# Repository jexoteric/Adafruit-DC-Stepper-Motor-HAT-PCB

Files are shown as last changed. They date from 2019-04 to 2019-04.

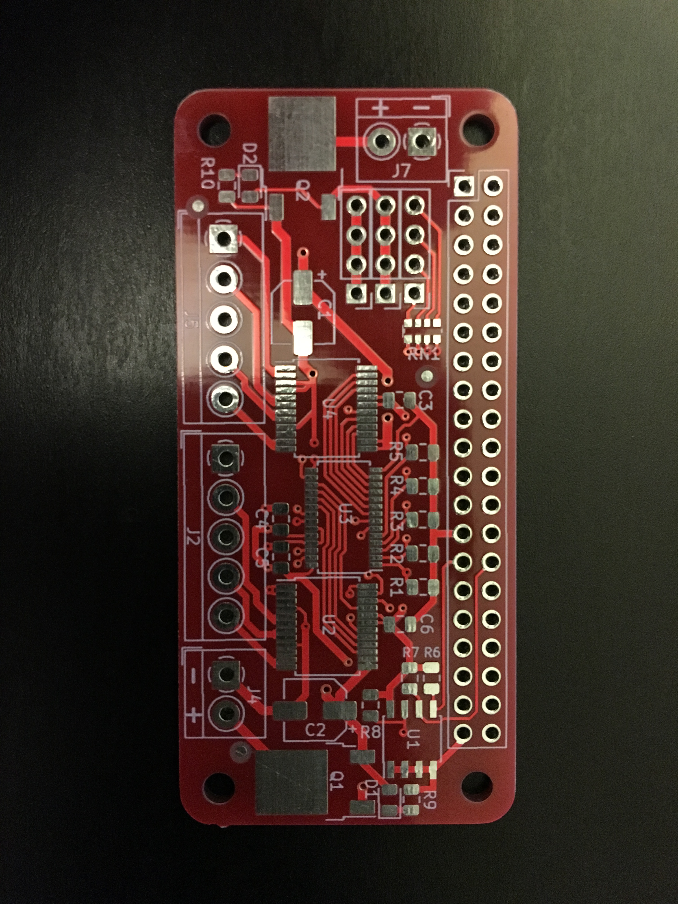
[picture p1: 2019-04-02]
IMG_0204.JPG

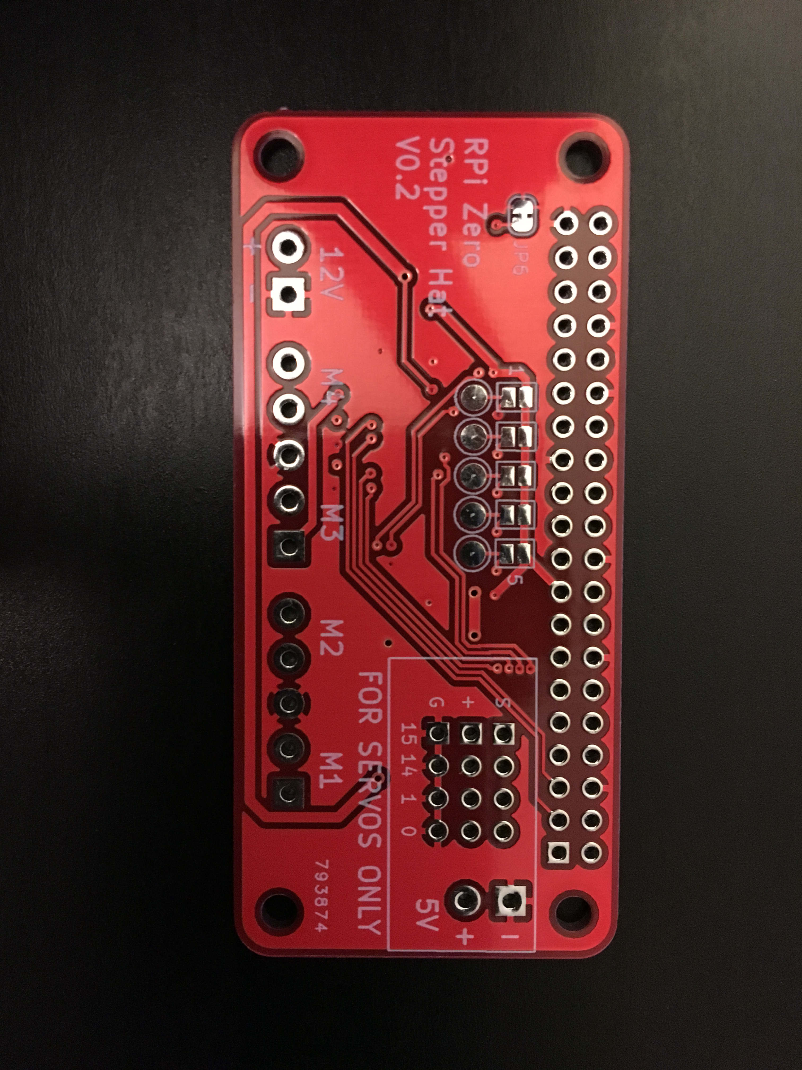
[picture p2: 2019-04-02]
IMG_0206.JPG

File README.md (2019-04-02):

# Raspberry Pi Zero DC and Stepper motor hat
Creating a more compact version of the Adafruit DC Stepper motor hat, with the goal of 100% compatability. The only real changes are there is no prototyping area or breakout of the pi pins. Optionally, the four extra PWM pins are now set up to control servos, using a seperate 5V power supply.

Programming with this board should be 100% identical to programming with the original Adafruit design linked below.

For more details, check out the product page at

   * https://www.adafruit.com/products/2348

Adafruit invests time and resources providing this open source design, 
please support Adafruit and open-source hardware by purchasing 
products from Adafruit!

Original board designed by Adafruit Industries.  
Creative Commons Attribution, Share-Alike license, check license.txt for more information
All text above must be included in any redistribution

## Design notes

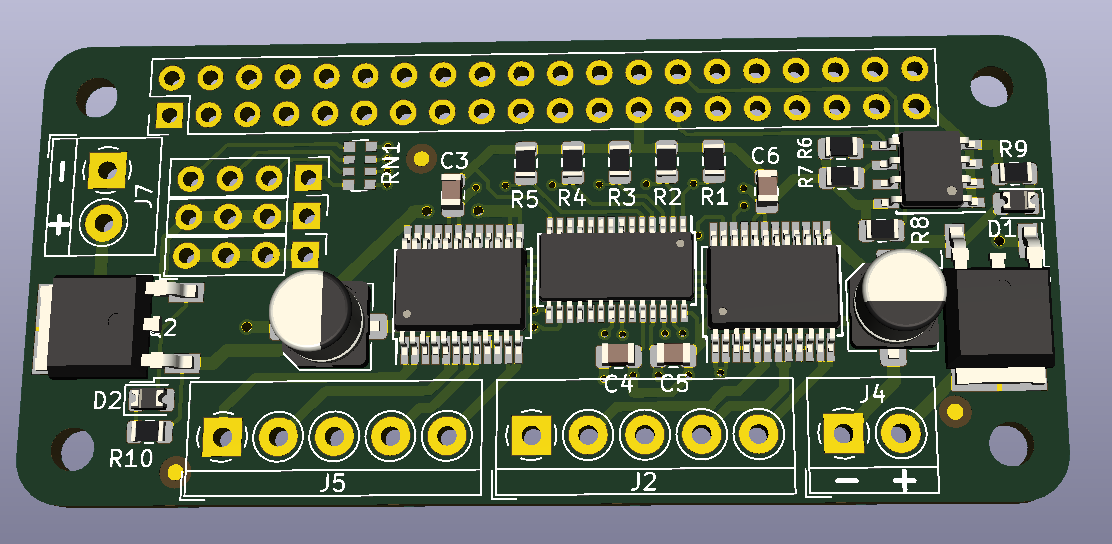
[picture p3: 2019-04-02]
pi_zero_stepper.PNG

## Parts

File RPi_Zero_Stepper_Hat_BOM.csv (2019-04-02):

Manufacturer Part Number | Manufacturer | Digi-Key Part Number | Customer Reference | Reference Designator | Packaging | Quantity | Unit Price | Extended Price | Description
EEE-1CA470WAR | Panasonic Electronic Components | PCE4588CT-ND | 47uF/16v | C1, C2 | Cut Tape (CT) | 2 | 0.38 | $0.76 | CAP ALUM 47UF 20% 16V SMD
CC0805ZKY5V6BB106 | Yageo | 311-1355-1-ND | 10uF | C3, C6 | Cut Tape (CT) | 2 | 0.28 | $0.56 | CAP CER 10UF 10V Y5V 0805
CC0805ZRY5V9BB104 | Yageo | 311-1361-1-ND | 0.1uF | C4, C5 | Cut Tape (CT) | 2 | 0.13 | $0.26 | CAP CER 0.1UF 50V Y5V 0805
17-21SYGC/S530-E2/TR8 | Everlight Electronics Co Ltd | 1080-1500-1-ND | GREEN | D1, D2 | Cut Tape (CT) | 2 | 0.3 | $0.60 | LED YELLOW/GREEN CLEAR 0805 SMD
AOD417 | Alpha & Omega Semiconductor Inc. | 785-1106-1-ND | AOD417 | Q1,Q2 | Cut Tape (CT) | 2 | 0.56 | $1.12 | MOSFET P-CH 30V 25A TO252
RNCF0805DTE10K0 | Stackpole Electronics Inc | RNCF0805DTE10K0CT-ND | 10K | R1, R2, R3, R4, R5 | Cut Tape (CT) | 5 | 0.17 | $0.85 | RES 10K OHM 0.5% 1/8W 0805
RC0805FR-073K9L | Yageo | 311-3.90KCRCT-ND | 3.9K | R6, R7, R8 | Cut Tape (CT) | 3 | 0.1 | $0.30 | RES SMD 3.9K OHM 1% 1/8W 0805
RNCP0805FTD1K00 | Stackpole Electronics Inc | RNCP0805FTD1K00CT-ND | 1K | R9 | Cut Tape (CT) | 1 | 0.1 | $0.10 | RES 1K OHM 1% 1/4W 0805
CAT24C32WI-GT3 | ON Semiconductor | CAT24C32WI-GT3CT-ND | CAT24C32 | U1 | Cut Tape (CT) | 1 | 0.2 | $0.20 | IC EEPROM 32K I2C 1MHZ 8SOIC
TB6612FNG,C,8,EL | Toshiba Semiconductor and Storage | TB6612FNGC8ELCT-ND | TB6612FNG | U2, U4 | Cut Tape (CT) | 2 | 2.11 | $4.22 | IC MOTOR DRIVER 2.7V-5.5V 24SSOP
PCA9685PW,118 | NXP USA Inc. | 568-11925-1-ND | PCA9685PW | U3 | Cut Tape (CT) | 1 | 2.33 | $2.33 | IC LED DRIVER RGBA 28-TSSOP
30035 | SCS | SCP417-ND | ESD Bag |  | Bag | 1 | 0.11 | $0.11 | BAG 3X5" ZIP STATIC SHIELD 1=1EA
SSQ-120-03-T-D | Samtec Inc. | SAM1204-20-ND | Stacking Header |  | Bulk | 1 | 3.53 | $3.53 | CONN RCPT 40POS 0.1 TIN PCB
ED555/2DS | On Shore Technology Inc. | ED1514-ND | Terminal Block 2pos | J4, J7 | Box | 2 | 1.06 | $2.12 | TERM BLK 2POS SIDE ENT 3.5MM PCB
ED555/5DS | On Shore Technology Inc. | ED1517-ND | Terminal Block 5pos | J2, J5 | Bulk | 2 | 1.72 | $3.44 | TERM BLK 5POS SIDE ENT 3.5MM PCB
EXB-38V221JV | Panasonic Electronic Components | Y9221CT-ND | Resistor Network | RN1 | Cut Tape (CT) | 1 | 0.1 | $0.10 | RES ARRAY 4 RES 220 OHM 1206
RC0805JR-07300RL | Yageo | 311-300ARCT-ND | 300 ohm resistor | R10 | Cut Tape (CT) | 1 | 0.1 | $0.10 | RES SMD 300 OHM 5% 1/8W 0805

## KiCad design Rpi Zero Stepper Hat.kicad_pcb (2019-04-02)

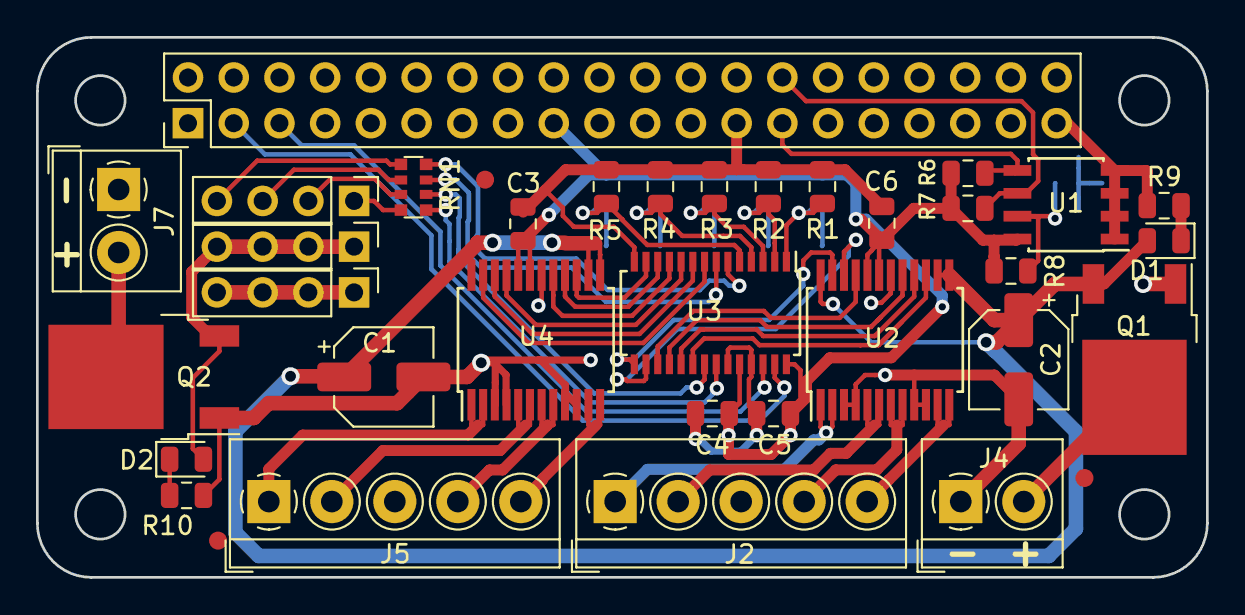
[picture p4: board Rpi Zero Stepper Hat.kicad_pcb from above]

Board: 2 copper layers, 65.0 x 30.0 mm, 44 parts (0 on the bottom side), 46 nets.

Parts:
+: Conn_01x05_Male; PinHeader_1x04_P2.54mm_Vertical
C1, C2: 47uF/16v; CP_Elec_5x5.4
C3, C6: 10uF; C_0805_2012Metric
C4, C5: 0.1uF; C_0805_2012Metric
D1, D2: GREEN; D_0805_2012Metric
G: Conn_01x04_Male; PinHeader_1x04_P2.54mm_Vertical
J1: Raspberry_Pi_2_3; PinHeader_2x20_P2.54mm_Vertical
J2, J5: Screw_Terminal_01x05; TerminalBlock_4Ucon_1x05_P3.50mm_Horizontal
J3: Conn_01x04_Male; PinHeader_1x04_P2.54mm_Vertical
J4, J7: Screw_Terminal_01x02; TerminalBlock_4Ucon_1x02_P3.50mm_Horizontal
JP1, JP2, JP3, JP4, JP5: SolderJumper_2_Open; SolderJumper-2_P1.3mm_Open_Pad1.0x1.5mm
JP6: SolderJumper_2_Bridged; SolderJumper-2_P1.3mm_Bridged_RoundedPad1.0x1.5mm
Q1, Q2: AOD417; TO-252-2
R1, R2, R3, R4, R5: 10K; R_0805_2012Metric
R6, R7, R8: 3.9K; R_0805_2012Metric
R9: 1K; R_0805_2012Metric
R10: 300; R_0805_2012Metric
RN1: R_Pack04; R_Array_Convex_4x0612
TP1, TP2, TP3, TP4, TP5: TestPoint; TestPoint_Pad_D2.0mm
U1: CAT24C32; SOIC-8_3.9x4.9mm_P1.27mm
U2, U4: TB6612FNG; SSOP-24_5.3x8.2mm_P0.65mm
U3: PCA9685PW; TSSOP-28_4.4x9.7mm_P0.65mm

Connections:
+3V3: C3.1, C4.1, C5.1, C6.1, J1.1, J1.17, JP1.2, JP2.2, JP3.2, JP4.2, JP5.2, R6.2, R7.1, R8.1, U1.8, U2.19, U2.20, U3.24, U3.28, U4.19, U4.20
+5V: +.1, +.2, +.3, +.4, D2.2, J1.2, J1.4, Q2.3
+12V: C1.1, C2.1, D1.2, Q1.3, U2.13, U2.14, U2.24, U4.13, U4.14, U4.24
A0: JP1.1, R1.1, TP1.1, U3.1
A1: JP2.1, R2.1, TP2.1, U3.2
A2: JP3.1, R3.1, TP3.1, U3.3
A3: JP4.1, R4.1, TP4.1, U3.4
A4: JP5.1, R5.1, TP5.1, U3.5
EECLOCK: J1.28, R7.2, U1.6
EEDATA: J1.27, R6.1, U1.5
GND: C1.2, C2.2, C3.2, C4.2, C5.2, C6.2, G.1, G.2, G.3, G.4, J1.6, J1.9, J1.14, J1.20, J1.25, J1.30, J1.34, J1.39, J2.3, J4.1, J5.3, J7.1, JP6.2, Q1.1, Q2.1, R1.2, R2.2, R3.2, R4.2, R5.2, R9.2, R10.2, U1.1, U1.2, U1.3, U1.4, U2.3, U2.4, U2.9, U2.10, U2.18, U3.14, U3.23, U3.25, U4.3, U4.4, U4.9, U4.10, U4.18
unnamed: D1.1, R9.1
unnamed: D2.1, R10.1
unnamed: J2.1, U2.1, U2.2
unnamed: J2.2, U2.5, U2.6
unnamed: J2.4, U2.7, U2.8
unnamed: J2.5, U2.11, U2.12
unnamed: J3.1, RN1.1
unnamed: J3.2, RN1.2
unnamed: J3.3, RN1.3
unnamed: J3.4, RN1.4
unnamed: J4.2, Q1.2
unnamed: J5.1, U4.1, U4.2
unnamed: J5.2, U4.5, U4.6
unnamed: J5.4, U4.7, U4.8
unnamed: J5.5, U4.11, U4.12
unnamed: J7.2, Q2.2
unnamed: JP6.1, R8.2, U1.7
PWM0: RN1.8, U3.6
PWM1: RN1.7, U3.7
PWM2: U3.8, U4.23
PWM3: U3.9, U4.22
PWM4: U3.10, U4.21
PWM5: U3.11, U4.17
PWM6: U3.12, U4.16
PWM7: U3.13, U4.15
PWM8: U2.23, U3.15
PWM9: U2.22, U3.16
PWM10: U2.21, U3.17
PWM11: U2.17, U3.18
PWM12: U2.16, U3.19
PWM13: U2.15, U3.20
PWM14: RN1.6, U3.21
PWM15: RN1.5, U3.22
SCL: J1.5, U3.26
SDA: J1.3, U3.27

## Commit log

2019-01-10 Add KiCAD Schematic
    Recreated the schematic in KiCAD using all native symbols.
    [Rpi Zero Stepper Hat.sch]
2019-04-02 V2 with 4x servo connections
    Revised design to use the extra pwm pins for servos with independent power input
    [Rpi Zero Stepper Hat.kicad_pcb, Rpi Zero Stepper Hat.sch]
2019-04-02 Added part number list as CSV file
    [RPi_Zero_Stepper_Hat_BOM.csv]
2019-04-02 Add Gerber Files and pictures
